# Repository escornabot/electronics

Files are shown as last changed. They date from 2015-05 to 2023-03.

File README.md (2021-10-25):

## Catalog
- [Escorna CPU][CPU01] is 50x50mm to 50x100mm board to use with Arduino Nano. It integrates keypad on board on 2x

- [Escorna_CPU_2_4][CPU240] It is a pcb that integrates an ATmega328P, a step-up (to use 1.2V batteries) and the rest of the electronics needed to build an Escornabot.

- [Arduino Shield][ARD01] is an Arduino Uno compatible
  shield ready to use with the Escornabot's motors and also integrates a keypad.

- [Cervus][CER01] is a board based on powerful ATmega32u4
  microcontroler and compatible with Arduino shields.
- [E_Keypad][KEY01] Is a 50x50mm board with 6  and 5 buttons and
  connects to any Escornabot.

- [E_KEY_BT][E_KEY_BT] Escornabot keyboard with MakeyMakey type sensors on the E_KEY_BT board.
   Any object that is minimally conductive can be used. Adjusting the value
   threshold: higher for less sensitivity, nothing needs to be changed in the
   robot firmware.

- [E_KEY_FICHA][E_KEY_FICHA] It allows the programming of Escornabot using printed or cut-out cards (cardboard ..) communicating the commands via Bluetooth.
  using @arduino Nano, easy to print, manageable and expandable to 15 "Tabs" thanks to the firmware of @caligari_pub

- [escoRnaFID][RnaFID]PCB for the project for children with visual impairment or blindness,
  developed by Angel Villanueva [@avilmaru][@avil] to control an Escornabot with RFID cards

## License

Every content in this repo, otherwise specified under subdirectories, is
licensed under [Creative Commons BY-SA][LICENSEcc] or [CERN Open Hardware Licence -W- V2][OHL-W-V2].
(by [XDeSIG][XDE01])

## To buy boards

Developer don't produce boards to sell. Under [_provider_][provider]
directory there are instructions to order yourself.

Are you a board provider? Please, send us your buyer's guide! :-)

[CPU01]: EscornaCPU
[CPU240]: https://github.com/xdesig/escornabot-electronics/tree/master/Electronics/EscornaCPU/2.x/2.40
[ARD01]: ArduinoShield
[CER01]: Cervus
[KEY01]: E_KEYPAD
[RnaFID]: escoRnaFID
[E_KEY_BT]: E_KEY_BT
[@avil]: https://twitter.com/avilmaru
[XDE01]: https://twitter.com/xdesig
[provider]: https://www.pcbway.com/project/member/?bmbno=6FE4DE76-9D11-4C
[LICENSEcc]: https://creativecommons.org/licenses/by-sa/3.0/es
[OHL-W-V2]: https://ohwr.org/project/cernohl/wikis/Documents/CERN-OHL-version-2

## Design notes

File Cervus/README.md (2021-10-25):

# Cervus 2.001

## Catalog

- [Cervus][KEY01] (by [Xdesig][XDE01]) is a 50x50mm board, it controls any Escornabot, and is an atmega development PCB (Arduino Leonardo compatible)

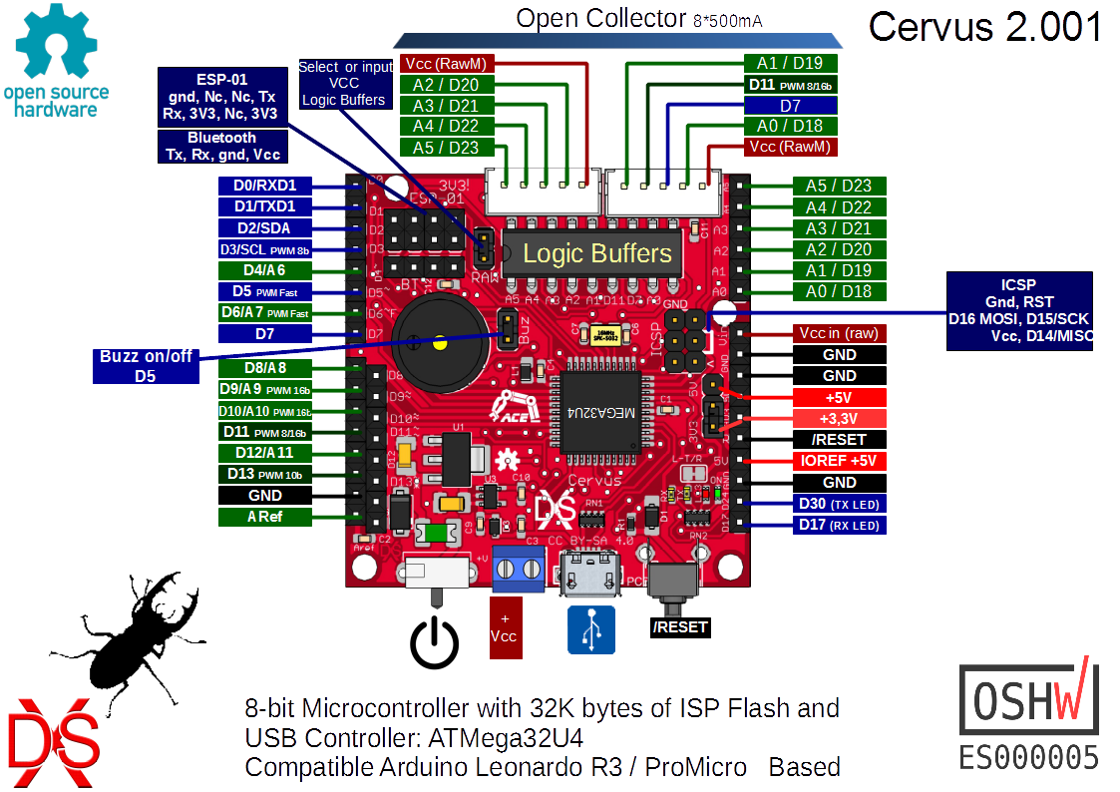
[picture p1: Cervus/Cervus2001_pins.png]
Top view


## License

Every content in this repo, otherwise specified under subdirectories, is
licensed under [Creative Commons BY-SA](LICENSE).

## To buy boards

Developers don't produce boards to sell. Under [PCBWAY]

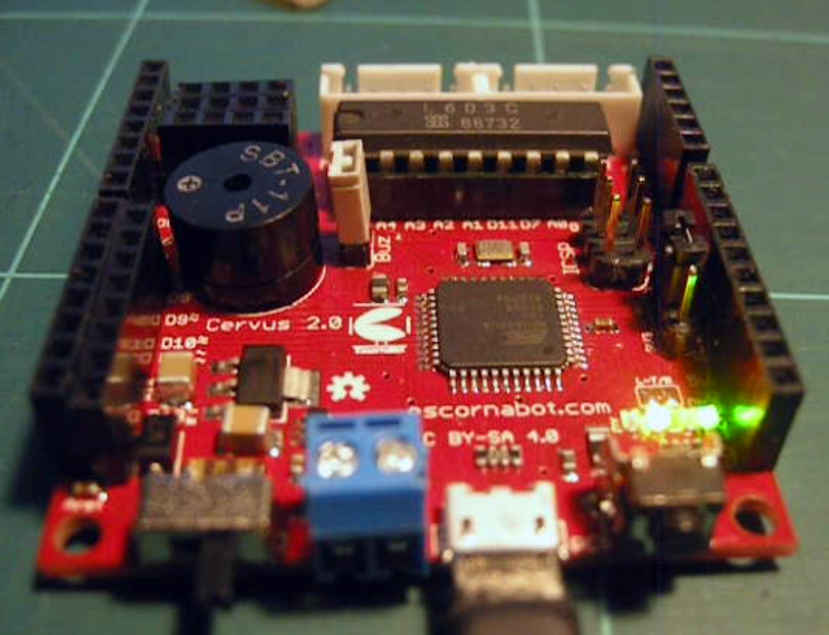
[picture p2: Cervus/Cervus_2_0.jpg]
Bottom view


[KEY01]: Keypad
[PCBWAY]: https://www.pcbway.com/project/shareproject/Cervus_Arduino_Leonardo_Coompatible.html
[XDE01]: https://twitter.com/xdesig

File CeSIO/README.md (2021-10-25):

# CeSIO Cervus Shield I/O  V 000

A pcb with all the I / O of Cervus (compatible with Arduino PCBs), available in connectors accompanied by + V and Gnd, whereby groups we can choose how we feed it: a + 5V, A + 3.3V or external V, giving the possibility to connect elements such as sensors, servos and other devices, has connector for ESP01 and Bluetooth.

It allows to use the DD05CVSA module to control a Li-ion battery.

Buy PCB in [PCBWAY]

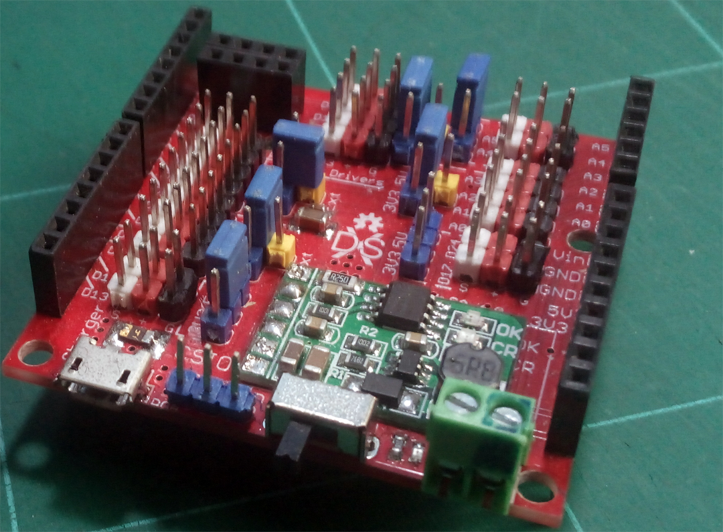
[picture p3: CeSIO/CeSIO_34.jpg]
Top view

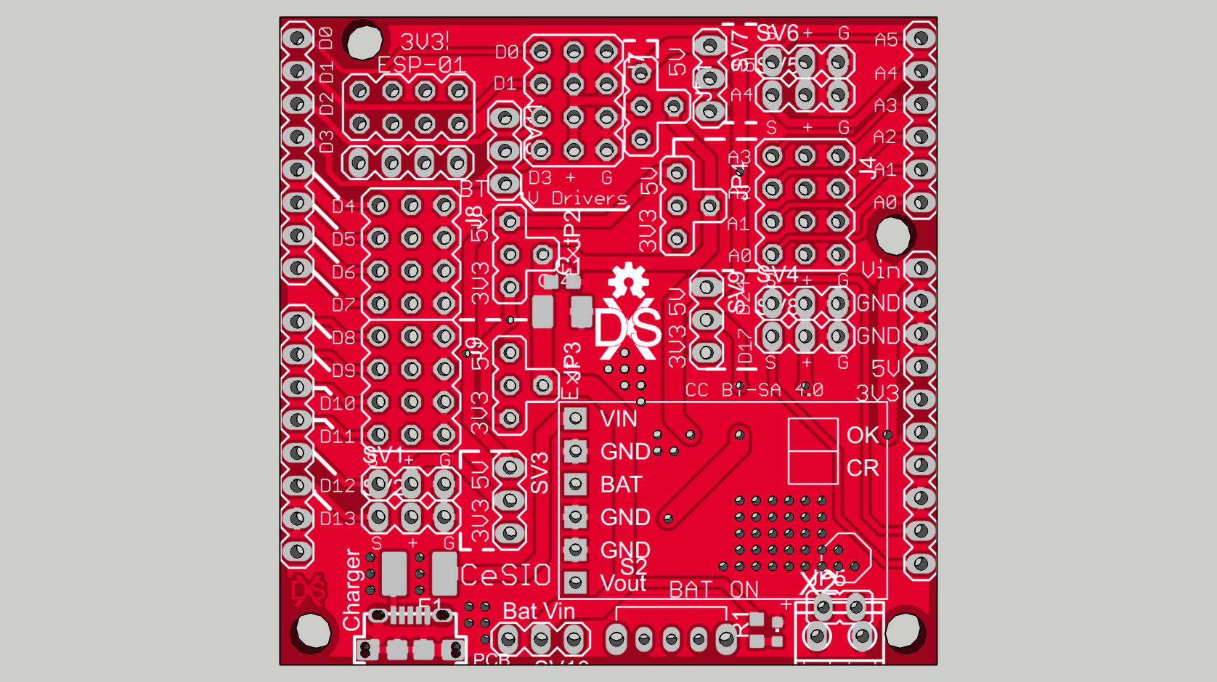
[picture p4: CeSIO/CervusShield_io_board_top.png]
Render

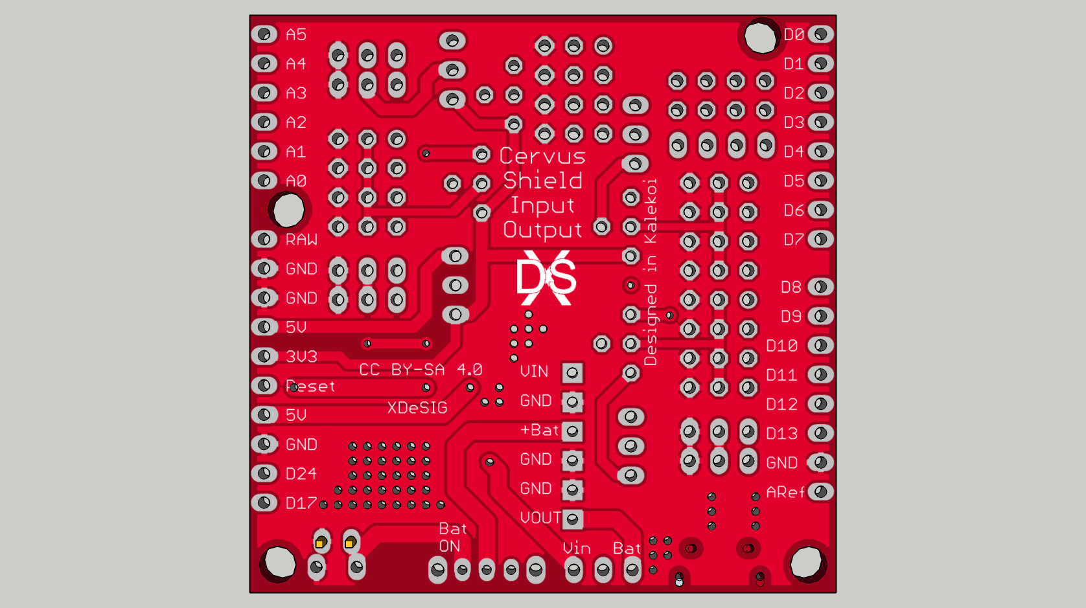
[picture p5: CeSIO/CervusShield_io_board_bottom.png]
Real


## Author and license
* Author: [XDeSIG][TWI01]
* License: [Attribution-ShareAlike 4.0 International] [CCBY-SA4.0]

<!-- links -->

[CCBY-SA4.0]: http://creativecommons.org/licenses/by-sa/4.0/
[TWI01]: https://twitter.com/xdesig
[PHT]: CeSIO_34.jpg
[RENDER]: CervusShield_io_board_top.png
[Real]: CervusShield_io_board_bottom.png
[PCBWAY]: https://www.pcbway.com/project/shareproject/CeSIO_Cervus_Shield_I_O.html

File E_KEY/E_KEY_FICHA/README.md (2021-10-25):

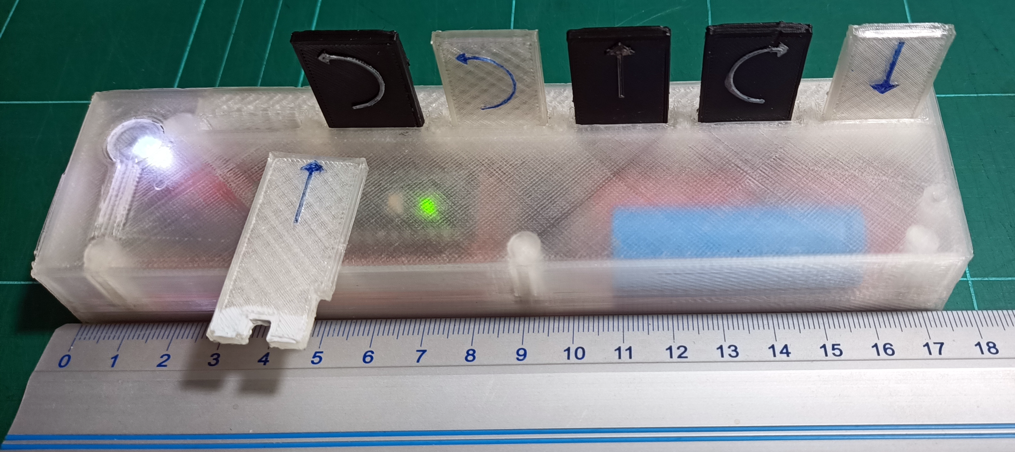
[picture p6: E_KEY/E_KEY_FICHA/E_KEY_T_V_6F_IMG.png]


## EscornabotFicha   
                     certification.oshwa.org/list.html
## E_KEY_FICHA (Tag)
It allows the programming of Escornabot using printed or cut-out cards (cardboard ..) communicating the commands via Bluetooth 
using @arduino Nano, easy to print, manageable and expandable to 15 "Tabs" thanks to the firmware of @caligari_pub.

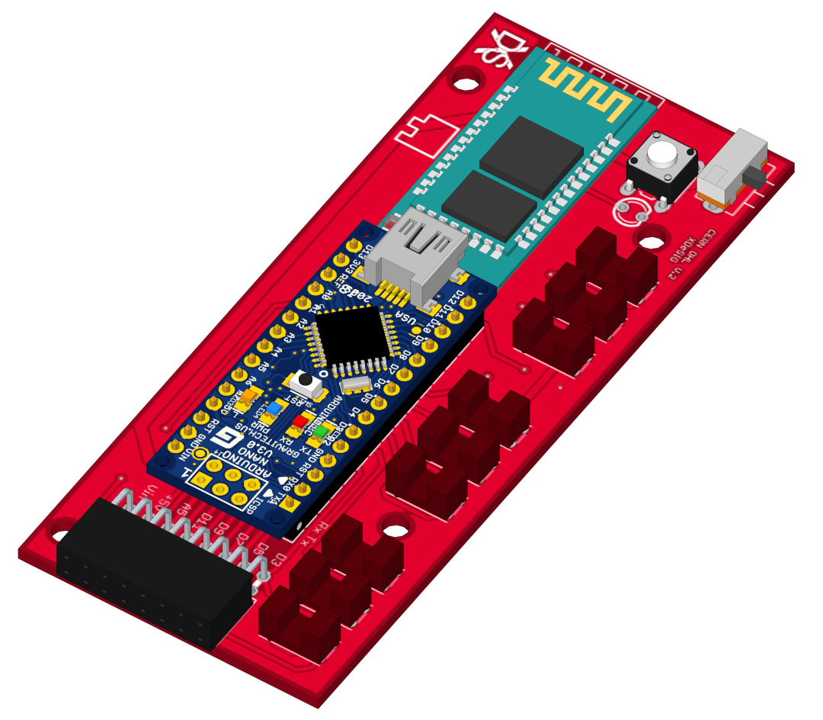
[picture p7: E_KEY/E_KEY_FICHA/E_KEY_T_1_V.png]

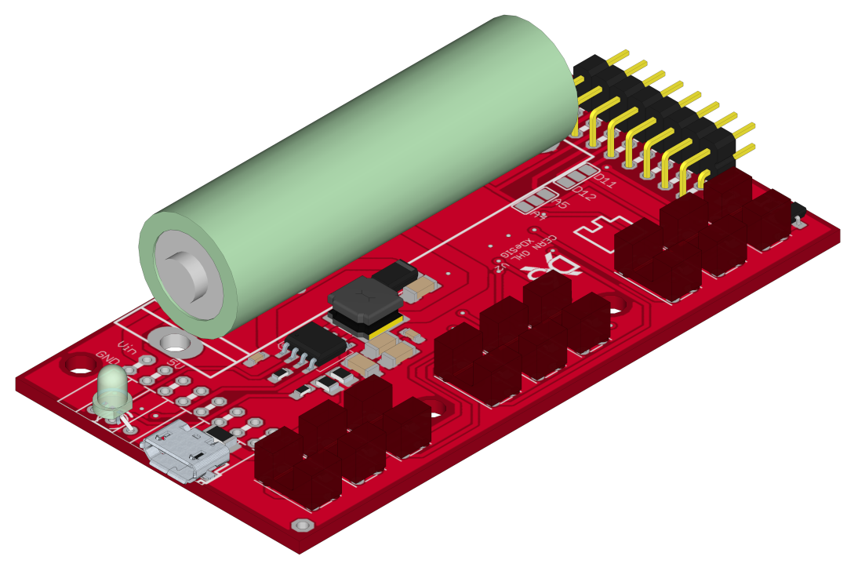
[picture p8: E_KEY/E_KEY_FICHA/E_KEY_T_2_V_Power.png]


## Number of Tags (Fichas)
To use six tags we need the PCBs E_KEY_T_1_V and E_KEY_T_2_V the latter with the power components.

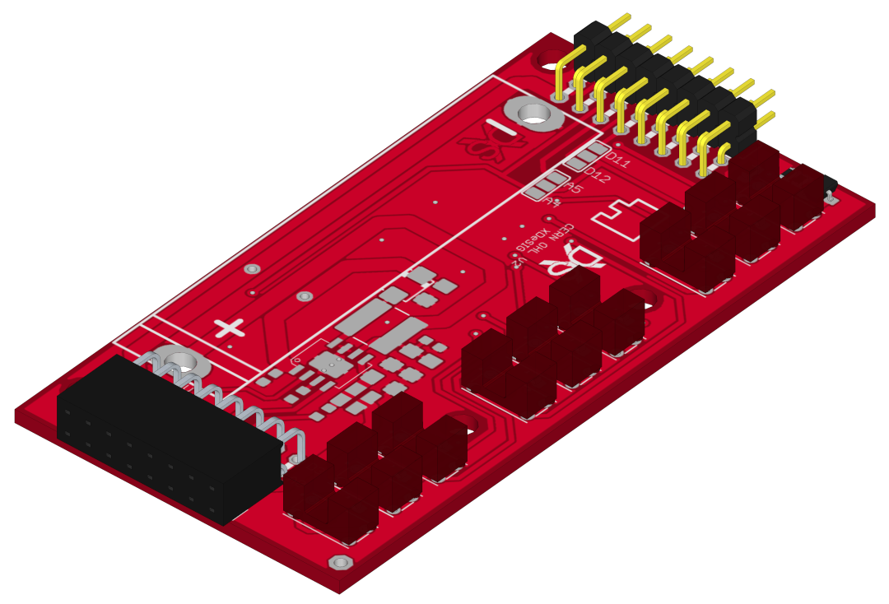
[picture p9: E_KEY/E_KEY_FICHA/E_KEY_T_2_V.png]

 If we want to have more chips (9 to 15) we will put intermediate circuits E_KEY_T_2_V without the power supply electronics.

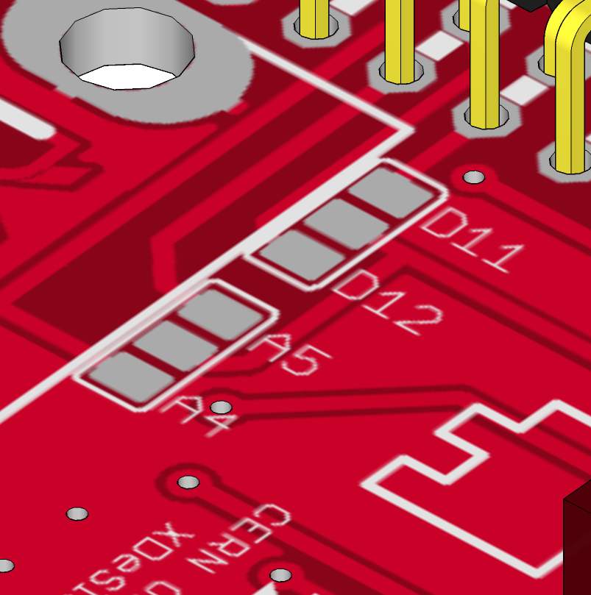
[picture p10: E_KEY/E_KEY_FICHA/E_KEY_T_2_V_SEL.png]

The selection will always be configured on the end plates, according to the firmware "configuration.h".
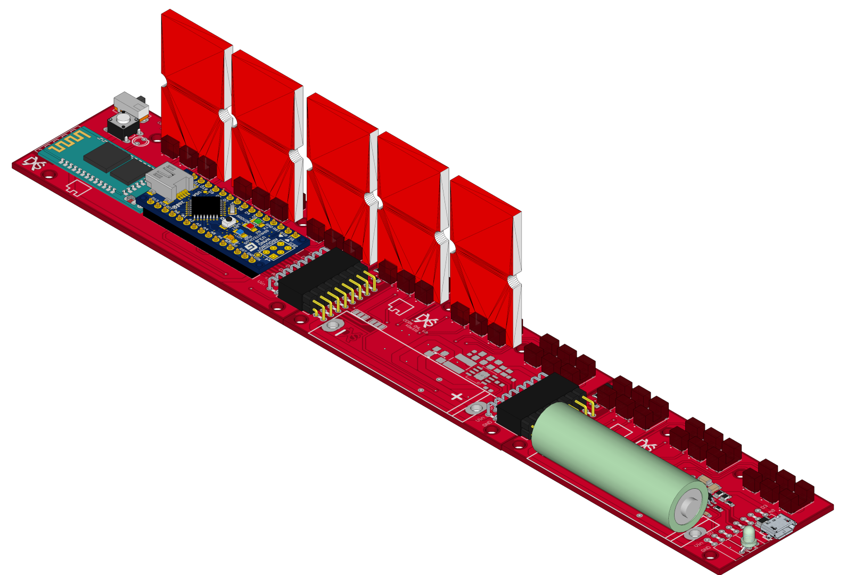
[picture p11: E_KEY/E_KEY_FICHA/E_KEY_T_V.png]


## License hardware and docu.

Every content in this repo, otherwise specified under subdirectories, is
licensed under [Creative Commons BY-SA][LICENSEcc] or [CERN Open Hardware Licence -W- V2][OHL-W-V2].
(by [XDeSIG][XDE01])

## License software.
  Copyright (C) 2020  Rafa Couto <caligari@treboada.net>
    This program is free software: you can redistribute it and/or modify
    it under the terms of the GNU General Public License as published by
    the Free Software Foundation, either version 3 of the License, or
    (at your option) any later version.
    This program is distributed in the hope that it will be useful,
    but WITHOUT ANY WARRANTY; without even the implied warranty of
    MERCHANTABILITY or FITNESS FOR A PARTICULAR PURPOSE.  See the
    GNU General Public License for more details.
    You should have received a copy of the GNU General Public License
    along with this program.  If not, see <https://www.gnu.org/licenses/>.

## Certification OSHWA [ES000024][OSHWAes000024]

## To buy boards

Developer don't produce boards to sell. Under [_provider_][provider]
directory there are instructions to order yourself.

Are you a board provider? Please, send us your buyer's guide! :-)

[imax]: https://github.com/xdesig/escornabot-electronics/blob/master/Electronics/E_KEY_BT/IMG_20180619_093516.jpg

[XDE01]: https://twitter.com/xdesig
[provider]:  http://
[LICENSEcc]: https://creativecommons.org/licenses/by-sa/3.0/es
[OHL-W-V2]: https://ohwr.org/project/cernohl/wikis/Documents/CERN-OHL-version-2
[OSHWAes000024]: https://certification.oshwa.org/es000024.html

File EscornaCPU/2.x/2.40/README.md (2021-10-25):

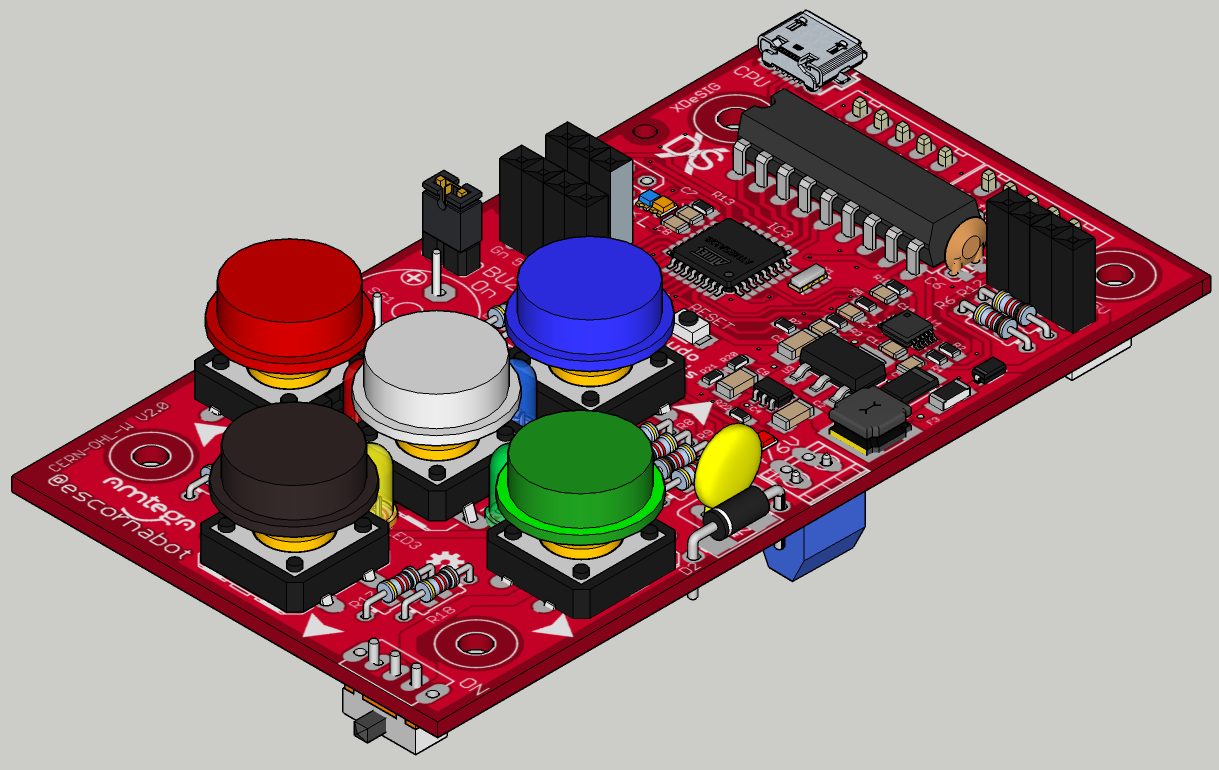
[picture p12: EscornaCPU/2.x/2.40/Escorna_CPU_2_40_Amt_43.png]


## Escorna CPU 2.4
This PCB integrates an ATmega328P, a step-up (great to use with 1.2V batteries, suggestion made by [caligari](https://github.com/rafacouto)) and the rest of the electronics needed to build a full-compatible Escornabot.
USB communications are supported by CH340E<br>
Arduino Uno, Arduino Nano compatible or ATmega minicore

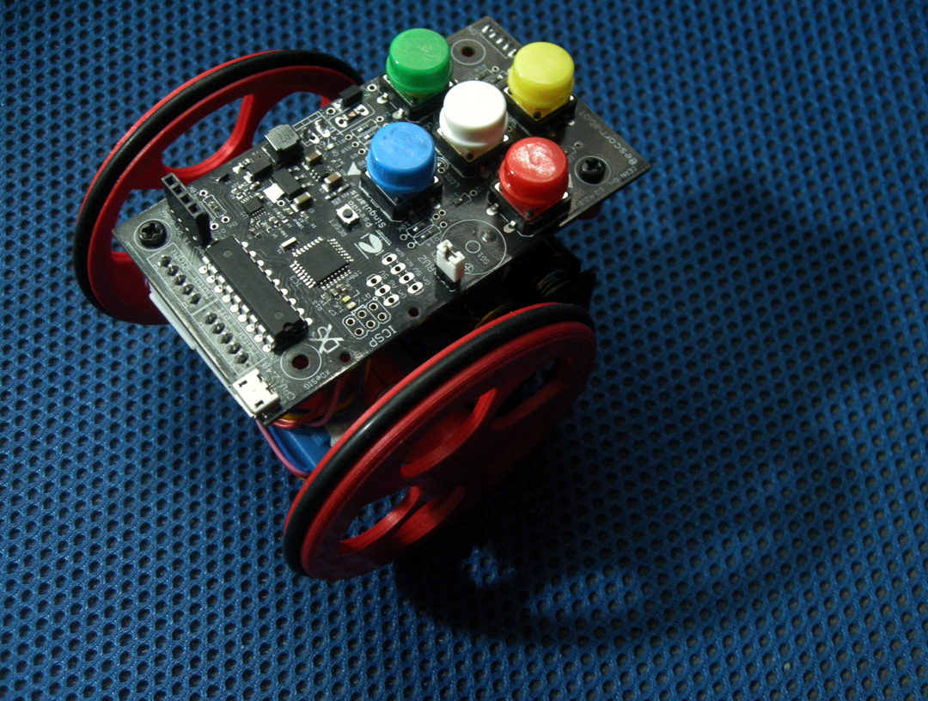
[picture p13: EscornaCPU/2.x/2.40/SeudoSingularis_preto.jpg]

   
## License



<br><br><br><br>

## Open Hardware Certification program



<br><br><br><br><br><br><br>

## To buy boards
Developer doesn't produce boards to get money. [_provider_][provider]

Are you a board provider? Please, send us your buyer's guide! xdesig@gmail.com

[XDE01]: https://twitter.com/xdesig
[provider]: https://www.pcbway.com/project/shareproject/Escorna_CPU_2_4.html
[LICENSEcc]: https://creativecommons.org/licenses/by-sa/3.0/es
[OHL-W-V2]: https://ohwr.org/project/cernohl/wikis/Documents/CERN-OHL-version-2

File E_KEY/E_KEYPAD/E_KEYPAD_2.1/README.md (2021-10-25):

# E_keyPad 2.10

## Catalog

- [Keypad][KEY01] (by [Xdesig][XDE01]) is a 50x50mm board with 5 buttons and
  connects to any Escornabot.

## License

Every content in this repo, otherwise specified under subdirectories, is
licensed under [Creative Commons BY-SA](LICENSE).

## To buy boards

Developers don't produce boards to sell. Under [PCBWAY]

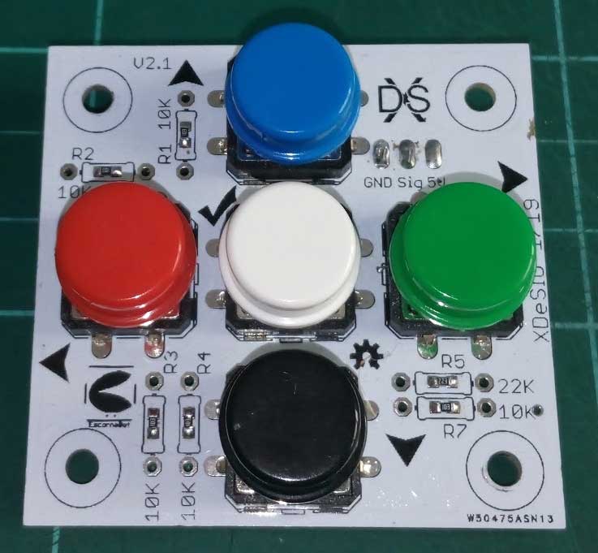
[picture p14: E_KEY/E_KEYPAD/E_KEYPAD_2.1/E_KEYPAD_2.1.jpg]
Bottom view


[KEY01]: Keypad
[PCBWAY]: https://www.pcbway.com/project/shareproject/W50475ASN5_Escorna_bot_2_1_Gerber.html
[XDE01]: https://twitter.com/xdesig

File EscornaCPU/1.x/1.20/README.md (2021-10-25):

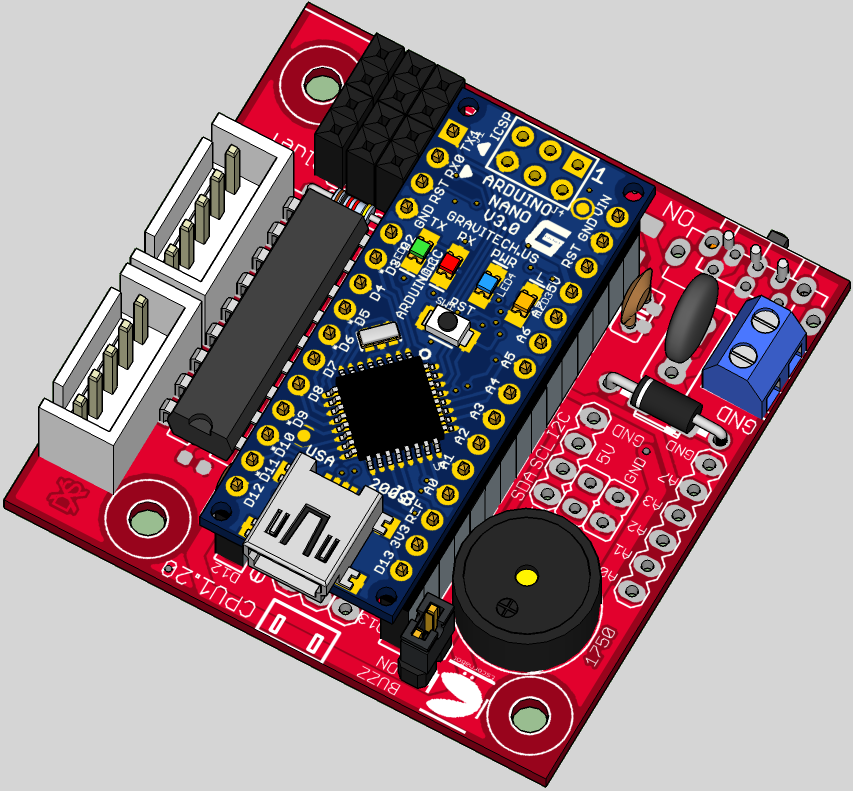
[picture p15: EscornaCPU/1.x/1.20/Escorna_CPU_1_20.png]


## Escorna CPU 1.20

It allows to include an Arduino Uno for the control of the robot, an ESP-01 or Bluetooth (for communications).
You can connect them to different keypads to manage the robot, I recommend the [E_KEYPAD_2.20]

## License

Every content in this repo, otherwise specified under subdirectories, is
licensed under [CERN Open Hardware Licence -W- V2][OHL-W-V2].
(by [XDeSIG][XDE01])

## To buy boards

Developer doesn't produce boards to get money. [provider]

Are you a board provider? Please, send us your buyer's guide! xdesig@gmail.com

[XDE01]: https://twitter.com/xdesig
[provider]: https://www.pcbway.com/project/shareproject/W50475ASN23_Escorna_CPU_1_20.html
[LICENSEcc]: https://creativecommons.org/licenses/by-sa/3.0/es
[OHL-W-V2]: https://ohwr.org/project/cernohl/wikis/Documents/CERN-OHL-version-2
[E_KEYPAD_2.20]: https://github.com/xdesig/escornabot-electronics/tree/master/Electronics/E_KEYPAD/E_KEYPAD_2.20

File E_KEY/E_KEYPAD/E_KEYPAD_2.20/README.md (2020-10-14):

# E_keyPad 2.20

## Catalog

- [Keypad][KEY01] (by [Xdesig][XDE01]) is a 50x50mm board with 5 buttons, 4 LEDs and
  connects to any Escornabot.

## License

Every content in this repo, otherwise specified under subdirectories, is
licensed under [Creative Commons BY-SA](LICENSE).
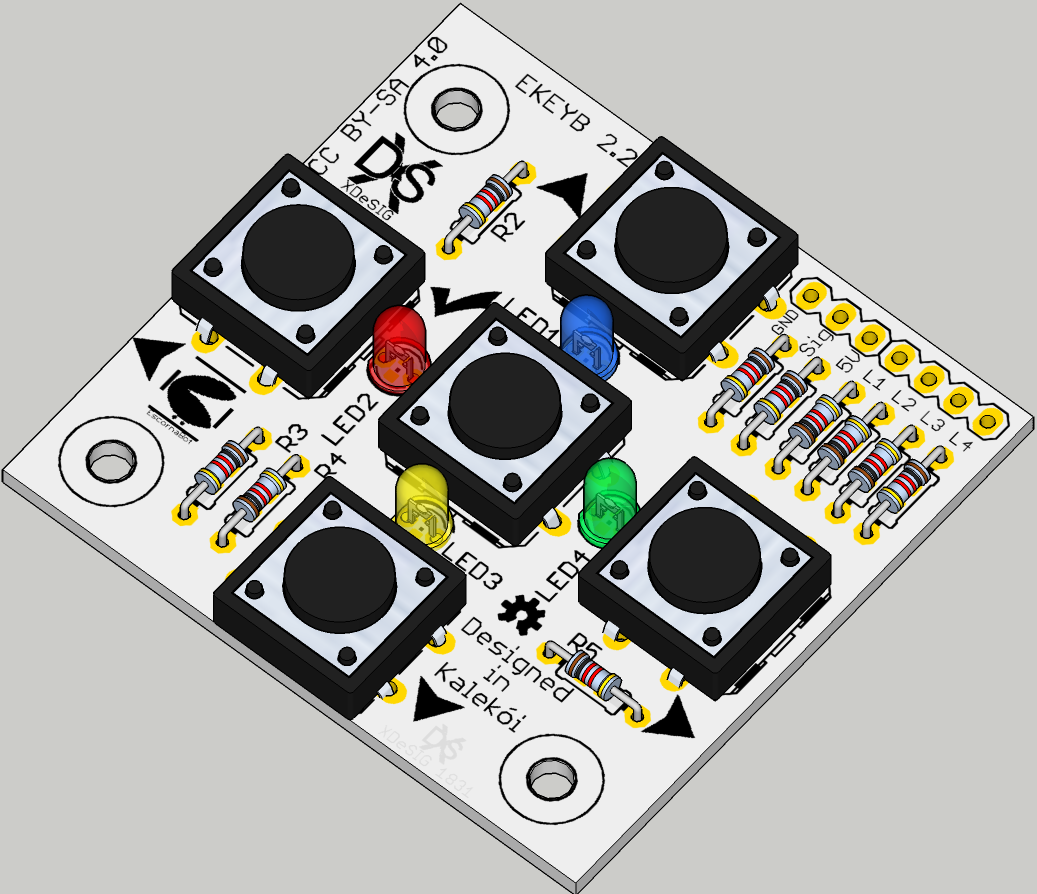
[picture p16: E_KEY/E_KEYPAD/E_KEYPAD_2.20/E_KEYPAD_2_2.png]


## To buy boards

Developers don't produce boards to sell. Under [PCBWAY]

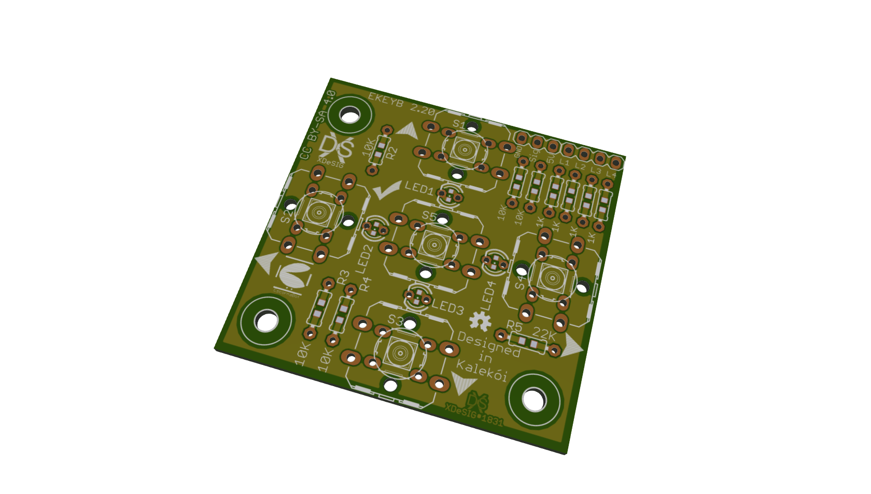
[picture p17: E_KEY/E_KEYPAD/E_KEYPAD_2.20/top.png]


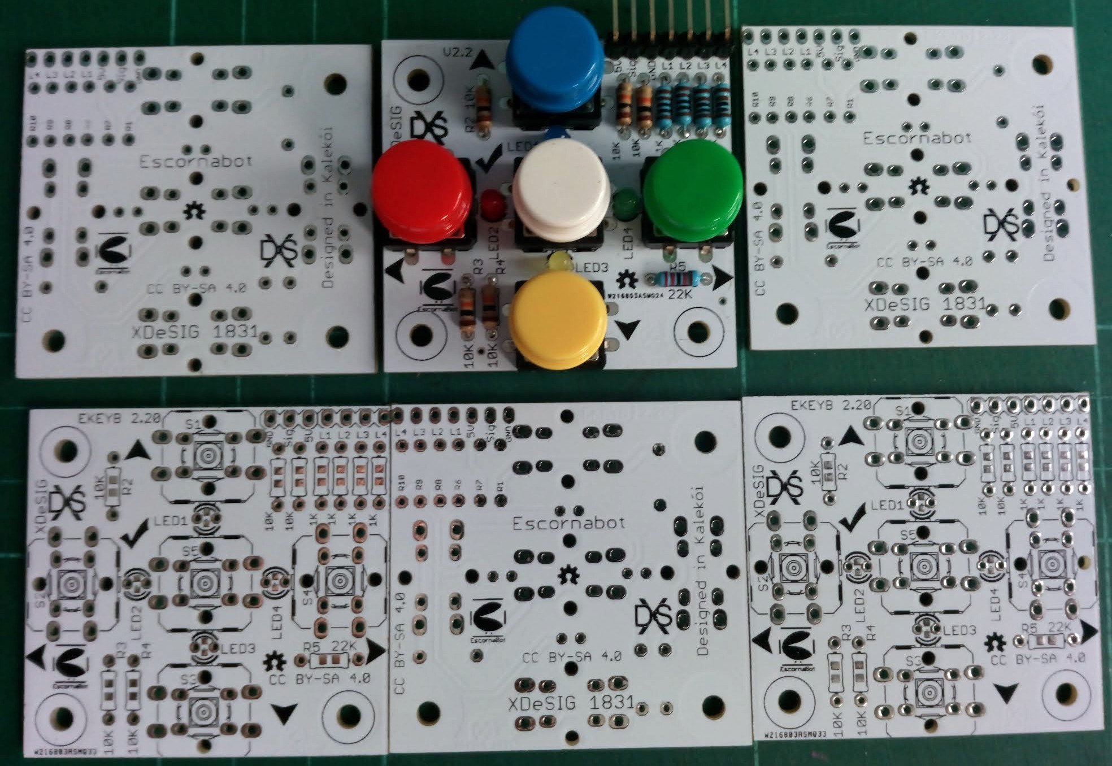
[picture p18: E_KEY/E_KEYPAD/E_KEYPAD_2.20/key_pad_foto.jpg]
Bottom view


[KEY01]: Keypad
[PCBWAY]: https://www.pcbway.com/project/shareproject/E_KEYPAD_2_2.html
[XDE01]: https://twitter.com/xdesig

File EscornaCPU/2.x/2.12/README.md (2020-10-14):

# EscornaCPU 2.12 by [XDesig][XDE01]

- Control of Escornabot through keyboard, Bluetooth HC-05, 06 and WiFi ESP-01.
- Central connector, for screen oled or I2C device.
- All components screen printed with your value.
- SMD (Surface Mount Device). or THT (through hole). Except the 3.3V and C1.2 regulator, 
- More info - [Caracteristicas\_CPU2\_12.pdf (in Galician)][NOT01]

- [Escorna\_CPU\_2\_12\_Gerber.zip (Gerber files)][GER01]
- [Escorna\_CPU\_2\_12.brd (Eagle Board)][BOA01]
- [Escorna\_CPU\_2\_12.sch (Eagle Schematics)][SCH01]
- [Escorna\_CPU\_2\_12\_ESQ.pdf (PDF Schematichs)][SCH02]
- [Escorna\_CPU\_2\_12\_measures.pdf (Board measures)][MEA01]

## License

Every content in this repo, otherwise specified under subdirectories, is
licensed under [Creative Commons BY-SA](LICENSE).

## To buy boards

Developer don't produce boards to sell. Under [PCBWAY]

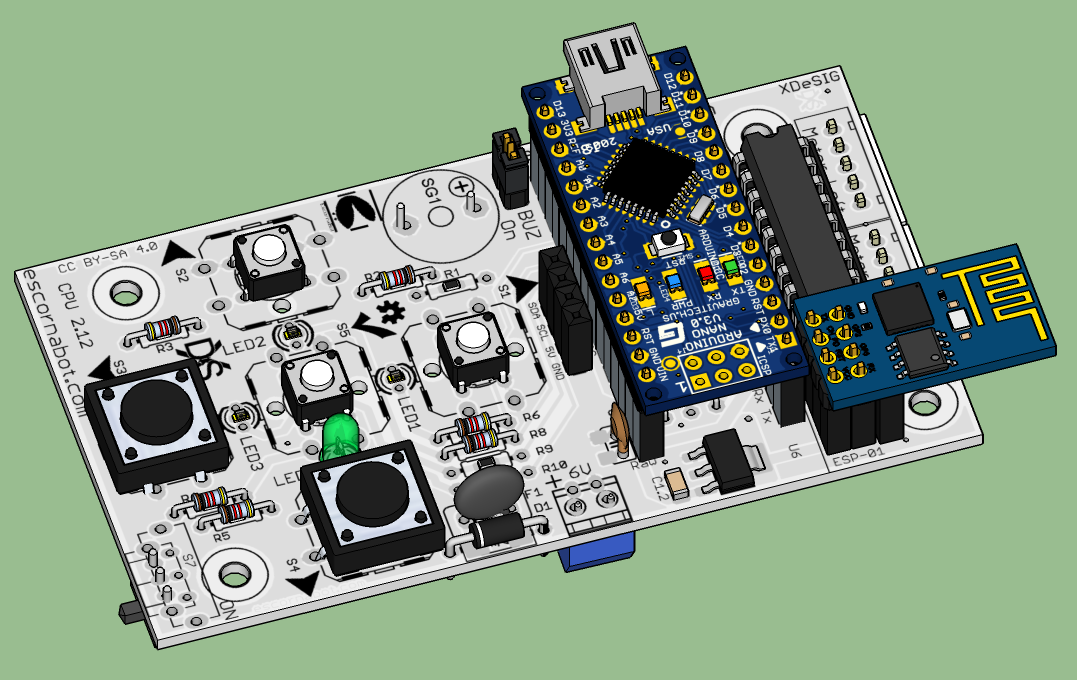
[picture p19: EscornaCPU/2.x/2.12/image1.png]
Top view

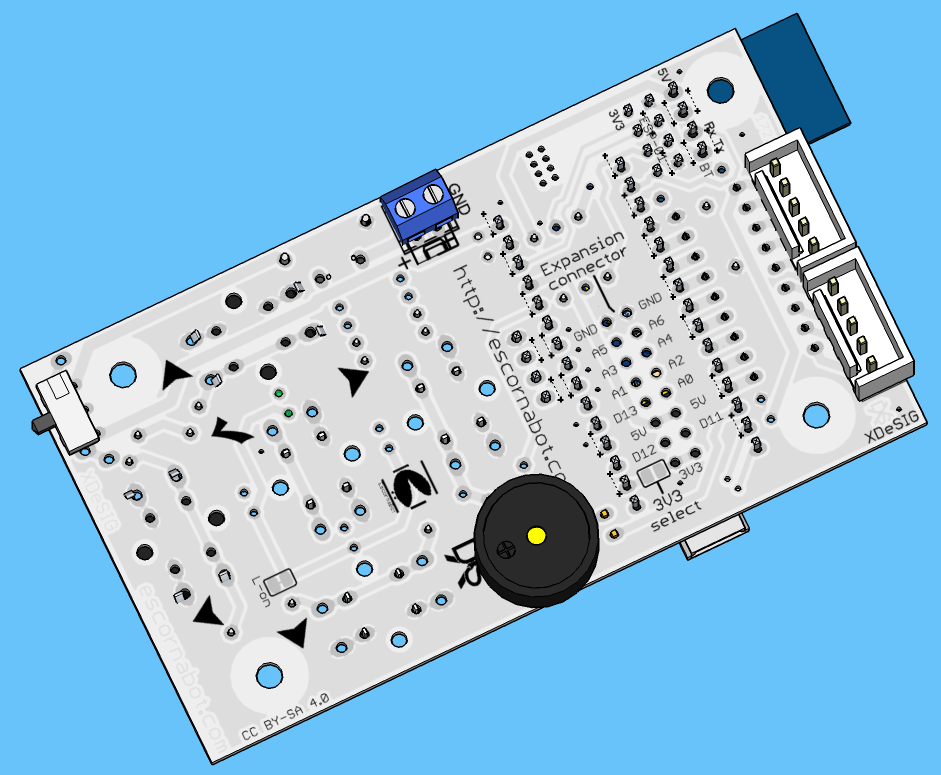
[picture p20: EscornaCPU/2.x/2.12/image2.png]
Bottom view


[GER01]: Escorna_CPU_2_12_Gerber.zip
[BOA01]: Escorna_CPU_2_12.brd
[SCH01]: Escorna_CPU_2_12.sch
[SCH02]: Escorna_CPU_2_12_ESQ.pdf
[MEA01]: Escorna_CPU_2_12_measures.pdf
[NOT01]: Caracteristicas_CPU2_12.pdf
[PCBWAY]: https://www.pcbway.com/project/shareproject/W50475ASN19_Escorna_CPU_2_12_Gerber.html
[XDE01]: https://twitter.com/xdesig

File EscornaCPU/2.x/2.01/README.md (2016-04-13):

# Escorna CPU + Keypad /  (version 2.10)

## Changes 2.10

  - Keyboard pin is A7 instead A4 so I2C interface is free to use in your projects.
  - Polarity inversion protection by diode anti-parallel and resetable fuse.
  - Power switch was moved to better position on the board 'backside'.
  - Switch compatibility with SK-12D07 and SK-12F14.
  - Keypad can use tactile switches 6mm, 12mm and 12mm with LED. See more below.
  - One of the EscornaShield connector was removed (obsolete).
  - Continuing the connector D13 - RAW (expand connections)
  - Buzzer, power connectors and drivers can be connected on both sides of the board.
  - Holes for holders continue in the same position (PCB extended 5.1mm backwards).
  - Full compatible one side, with an operative Escornabot (excepting the expansion connector).

## Tactile switches with LED

LED assignments:    --        [suggested color][wiki]

| KEY / signal| Color |
|---|---|
| UP  / A0 | Blue  |
| RIGHT / A3  | Gren  |
| DOWN / A2 | Yelow |
| LEFT / A1 | Reed  |
| GO / D13 | WiteA |

The LEDs can be disabled by cutting a small wire-jumper, you can use these outputs for other things. Reconnect with a small welding.

## Expansion connector

2.54mm double strip

| row 1 | row 2 |
|---|---|
| 3V3 | 3V3 |
| 5V | 5V |
| D13 / SCK | A0 / D14 |
| A1  / D15 | A2 / D16 |
| A3  / D17 | A4 / D18 / SDA |
| A5  / D19 / SCL | A6 / No Pullup |
| GND | GND |
|-----------------|----------------|

## Author and license

* Author: [XDeSIG][TWI01]
* License: [Creative Commons BY-SA][CCBYSA]

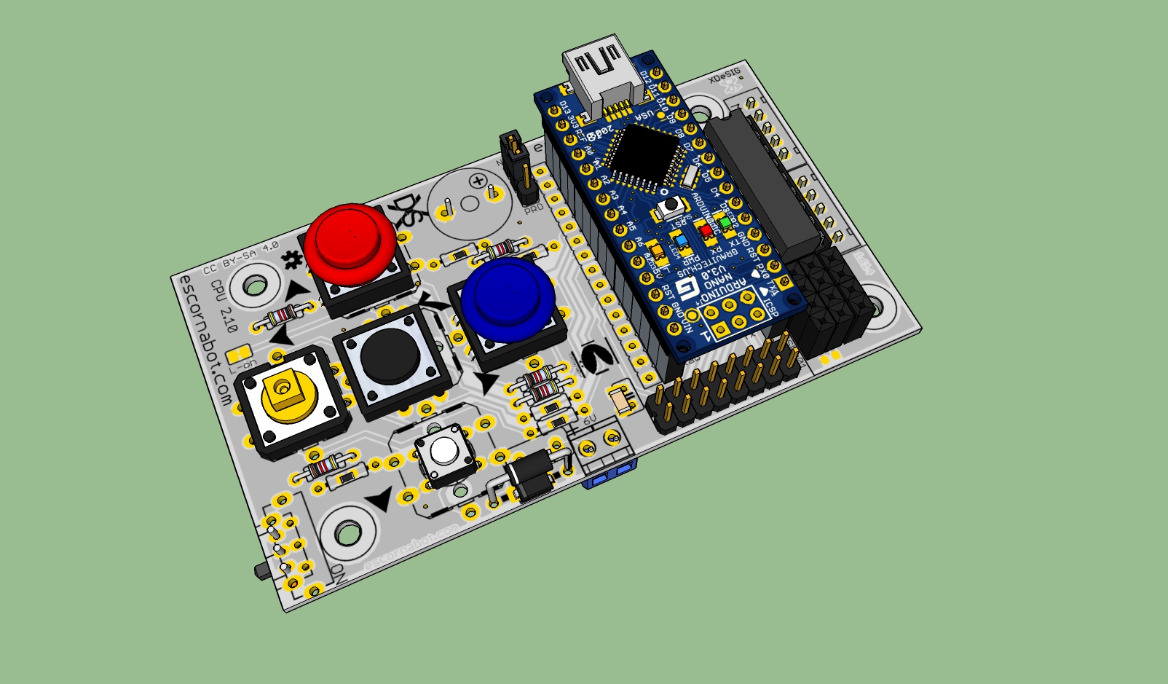
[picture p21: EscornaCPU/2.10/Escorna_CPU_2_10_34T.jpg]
Render Escorna CPU 2.10


<!-- links -->
[wiki]: https://en.wikipedia.org/wiki/Navigation_light
[CCBYSA]: http://creativecommons.org/licenses/by-sa/4.0/
[TWI01]: https://twitter.com/xdesig
[RENDER]: Escorna_CPU_2_10_34T.jpg

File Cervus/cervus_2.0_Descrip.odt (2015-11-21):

Zocalo ( tiras de pins esquerdo) 8 + 8 pins: Zocalo ( tiras de pins dereito) 6 +9 pins

Pin Atmega Leonardo Pin Atmega Leonardo

1 PD2 D0/RX 1 PF0 A5

2 PD3 D1/TX 2 PF1 A4

3 PD1 D2/SDA 3 PF4 A3

4 PD0 D3/SCL~ 4 PF5 A2

5 PD4 D4/A6~ 5 PF6 A1

6 PC6 D5 ~~ 16bits 6 PF7 A0

7 PD7 D6/A7 ~HSpeed

8 PE6 D7

8 RAW Vin

9 PB4 D8/A8 9 GND GND

10 PB5 IO9/A9 ~~ 16bits 10 GND GND

11 PB6 IO10/A10 ~~ 16bits 11 +5V +5V

12 PB7 IO11 ~~ 8/16Bits 12 +3V3 3.3V

13 PD6 IO12/A11~HSpeed 13 RESET RESET

14 PC7 IO13 ~10bits 14 +5V +5V

15 GND GND 15 D24/LTX N/C

16 Aref Aref 16 D17/LRX ( )

En grosa as conexións utilizadas por Escornabot.

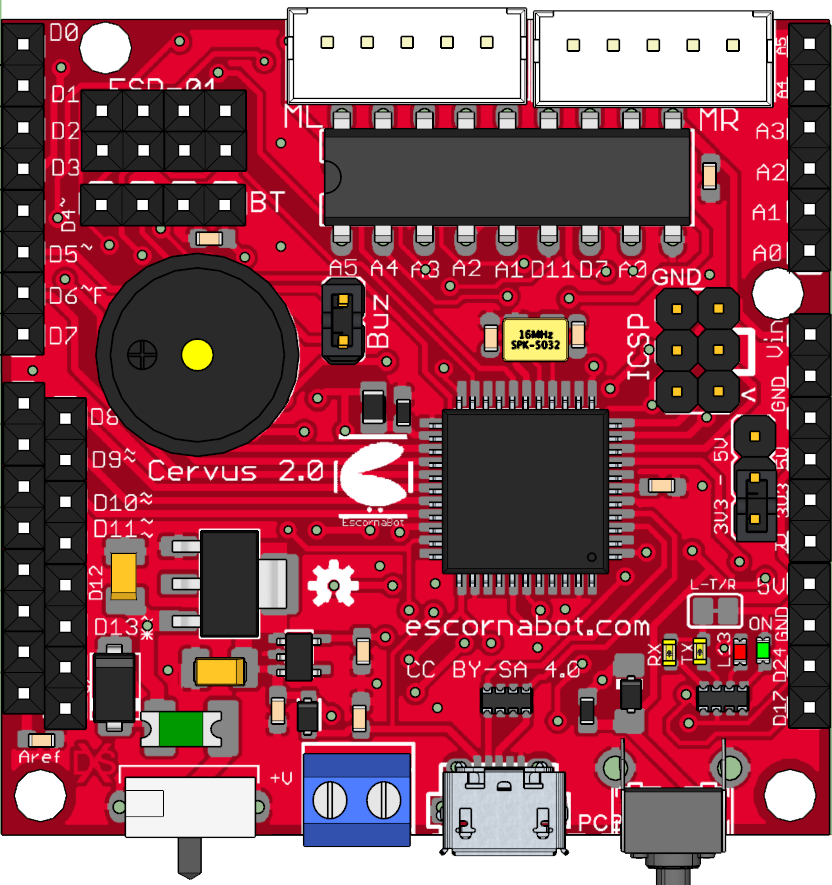
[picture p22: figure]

Selección de Alimentación 3,3V e 5V

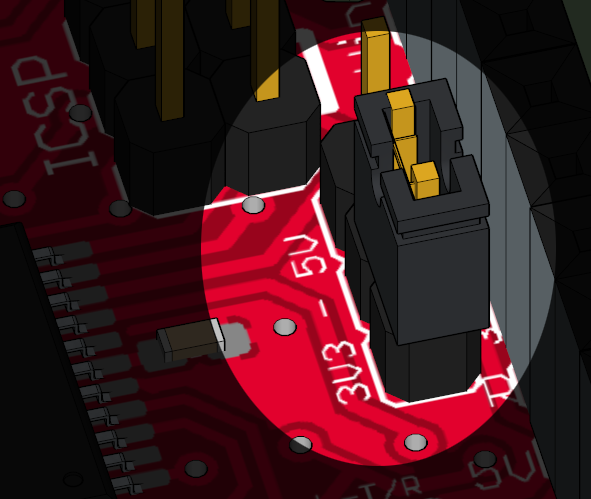
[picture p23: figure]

Posibilidade de descontar os leds ( LRX. LTX ) da placa para que non utilicen corrente das saídas ( D24, D17 ).

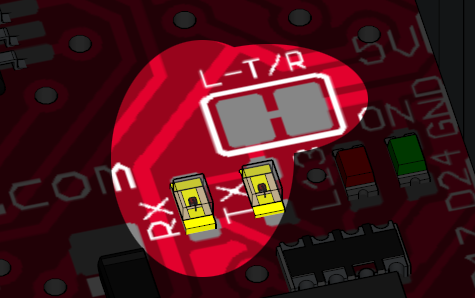
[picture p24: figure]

Igualmente co led L13 conectado a D13


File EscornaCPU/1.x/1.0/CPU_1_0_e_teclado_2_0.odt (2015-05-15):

Esquema - Escorna CPU 1.0 - Atallo os ficheiros: http://goo.gl/NUfwrV


JP1 Interruptor alimentación

JP2 podemos elixir onde conectar o Zoador,

Opcións: Sen ponte Modo silencioso (adestrar sen molestar os que durman ou estudan)

Ponte 1 – 2 Placas Pro-mini e Pro-micro

X3 conector teclado externo compatible ca versión 1 e 2, non é preciso cando se conecta o teclado Shield.

SV4 conector para modulo Bluetooth (ou outro que precise Tx e Rx)

Montaxe

Placa - Escorna CPU 1.0 -


Nota: Se se soldan os condensadores Cx non soldar os condensadores Cx.1

Dimensións Placa - Escorna CPU 1.0 -


O pad que se atopa (Baixo dereita) o lado de Tx de SV4 pode tradearse a 3mm para ter outro punto de amarre

Esquema - Escorna Shield botoneira 2.0B - Atallo os ficheiros: http://goo.gl/bZ2Vkc


Cando non utilizamos o teclado en modo shield podemos conectalo a placa CPU mediante J2. (ollo xa non teremos acceso o resto dos conectores led...)

SJ1 é un selector por soldadura para elixir a alimentación do conector J1

Opcións : 1 - 2 a tensión no pin 5 é a de entrada (RAW).

2 - 3 a tensión no pin 5 é a regulada polo arduino (5Vcc)

Montada independente Montada como Shield


Escorna CPU 1.0 e Botoneira 2.0 (shield) + Ideas

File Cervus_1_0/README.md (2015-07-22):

# Cervus version 1.0

* Author: [XDeSIG][SITE]
* License: [Creative Commons BY-SA][CCBYSA]

Render EscornaShield Keypad

[CCBYSA]: http://creativecommons.org/licenses/by-sa/4.0/
[SITE]: https://sites.google.com/site/xdesig/
[RENDER]: Cervus_1_0.jpg

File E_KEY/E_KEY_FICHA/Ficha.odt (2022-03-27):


Tamaño orientativo


Codificación da fichas (axustable en configuration.h)

W

1 2 3

Cortes

Función | Corte 1 | Corte 2 | Corte 3 | Code_
Inicio (sen ficha) | | | | 0
E | | | | 1
s | | | | 2
e | | | | 3
W | | | | 4
n | | | | 5
w | | | | 6
G | | | | 7

Escorna Ficha

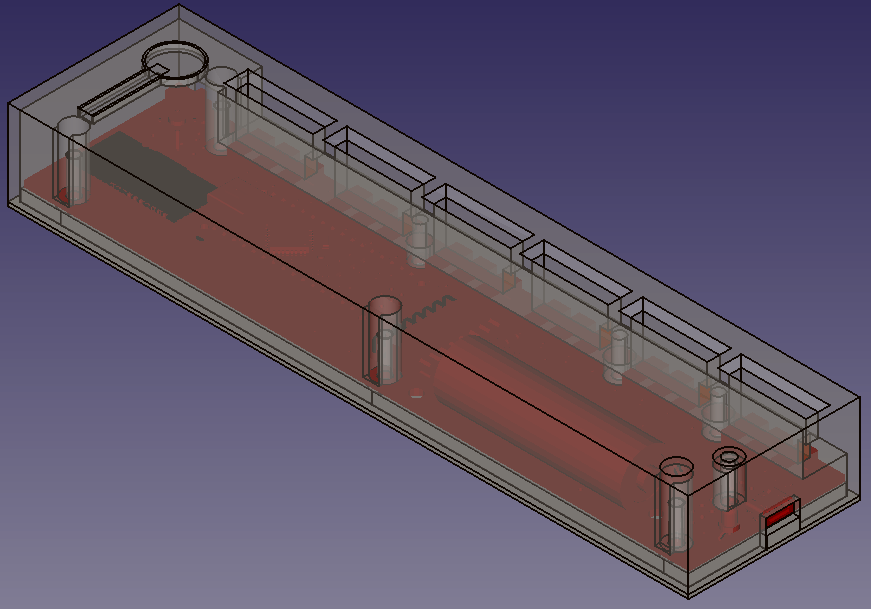
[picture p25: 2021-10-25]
E_KEY/E_KEY_FICHA/E_KEY_T_V_6F.png

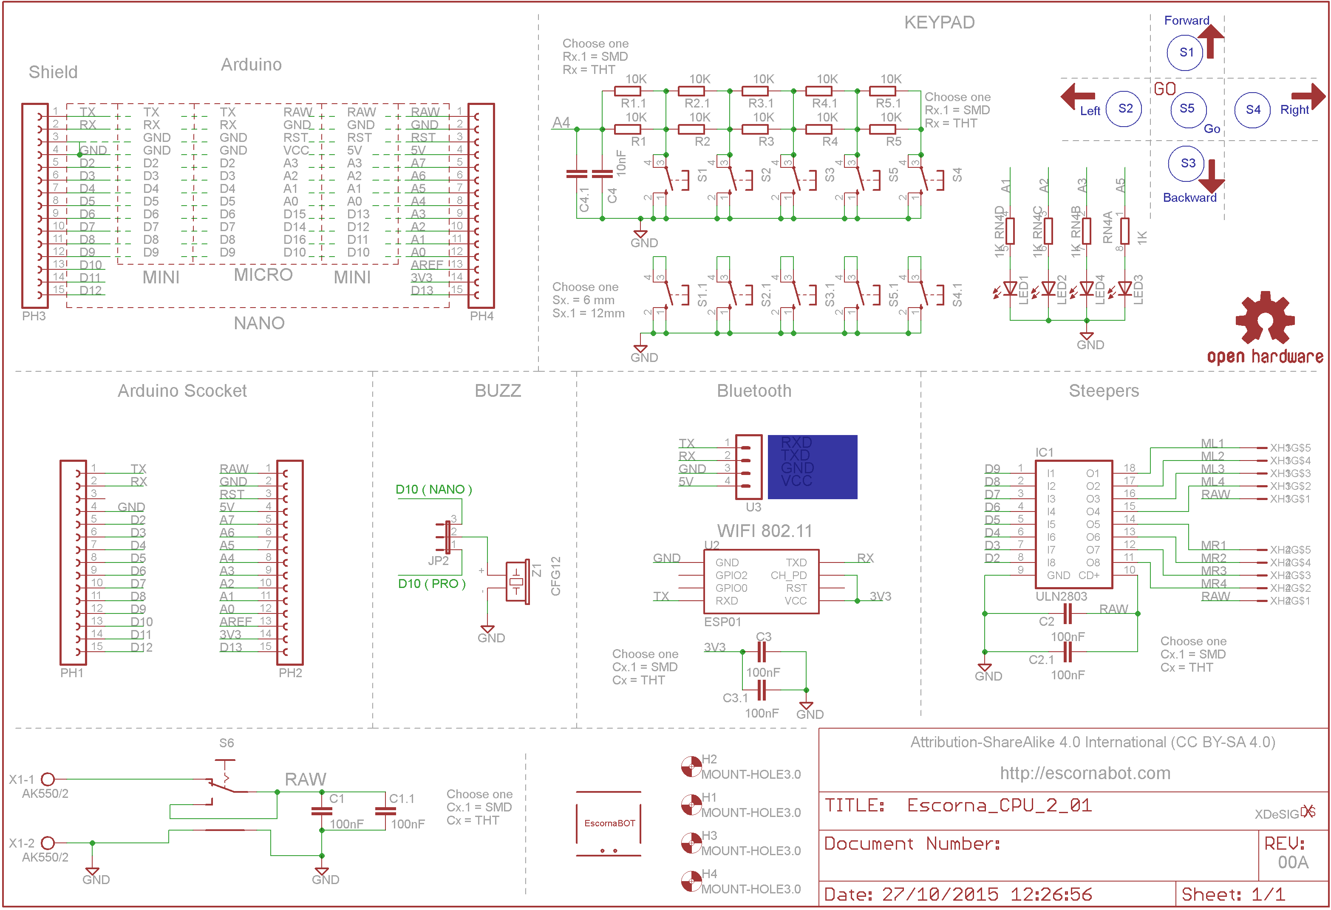
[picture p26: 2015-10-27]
EscornaCPU/2.x/2.01/Escorna_CPU_2_01_esq.png

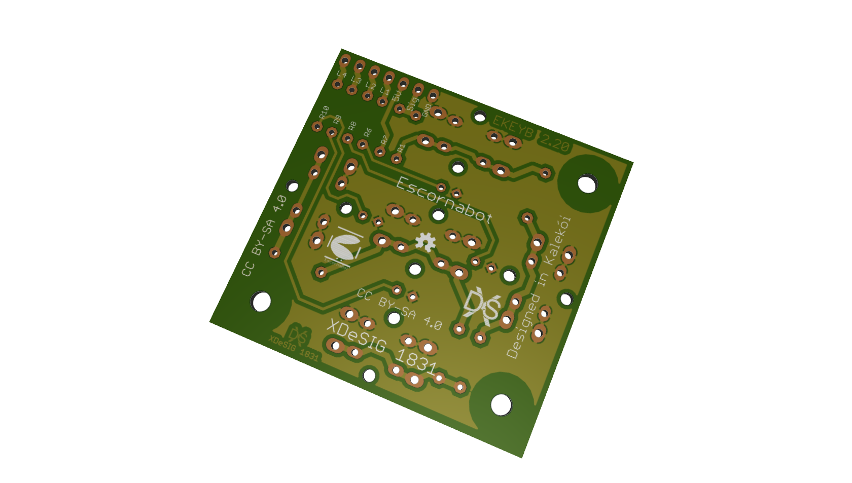
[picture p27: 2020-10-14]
E_KEY/E_KEYPAD/E_KEYPAD_2.20/bot.png

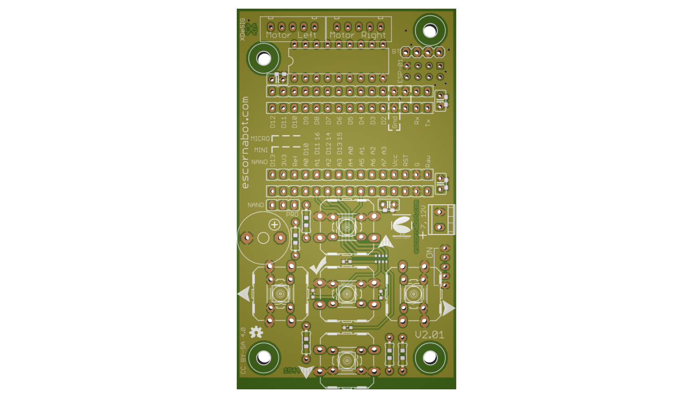
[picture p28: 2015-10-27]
EscornaCPU/2.x/2.01/Escorna_CPU_2_01_Top.png

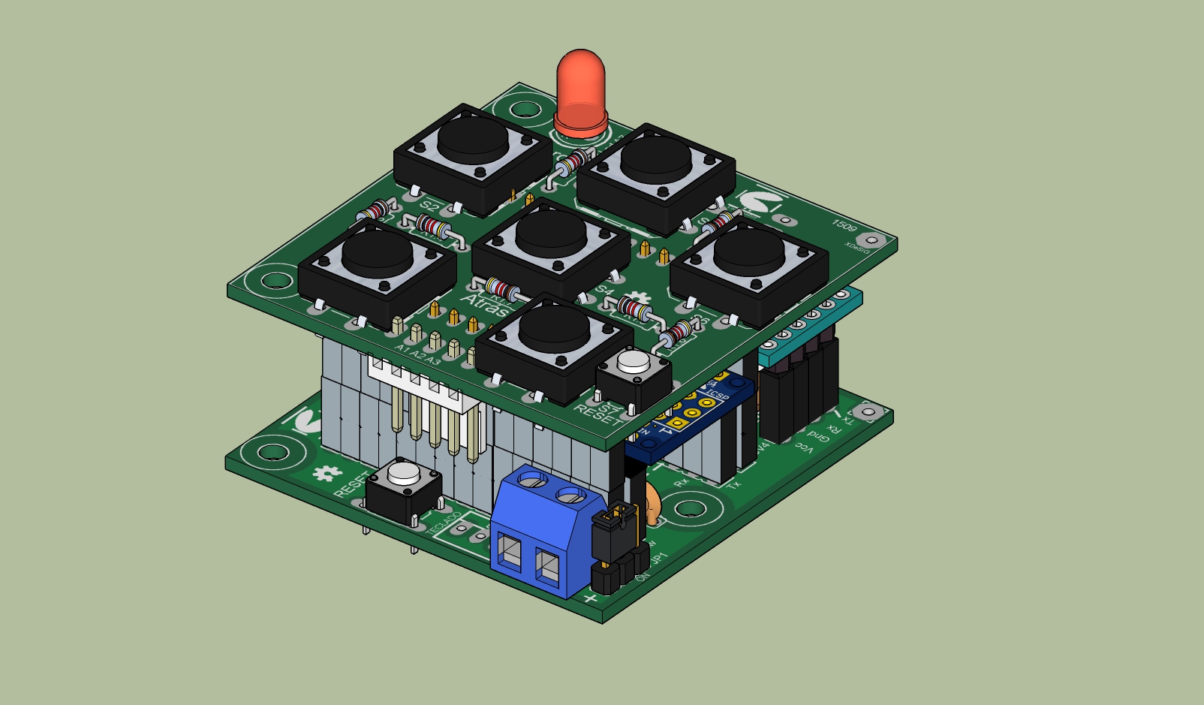
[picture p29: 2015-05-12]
EscornaCPU/1.x/1.0/Escorna_CPU_1_0 -BotoneiraShield_2_0.jpg

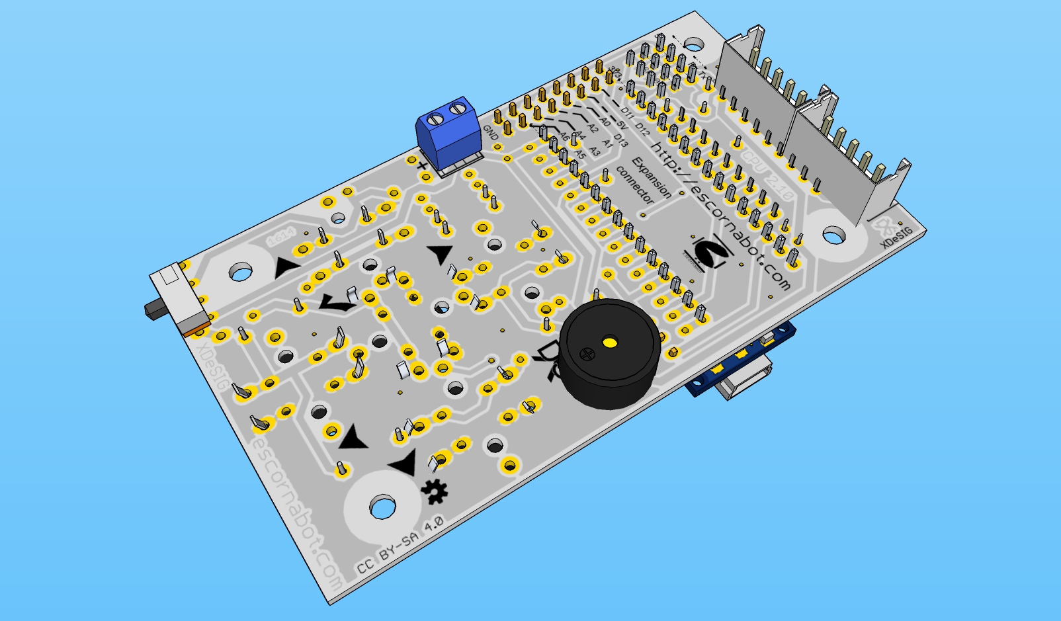
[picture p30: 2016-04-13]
EscornaCPU/2.x/2.10/Escorna_CPU_2_10_34B.jpg

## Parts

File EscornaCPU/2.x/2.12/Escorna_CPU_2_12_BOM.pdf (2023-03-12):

### Escorna_CPU_2_12_BOM

### “XDESIG”

Escornabot CPU 2.12

Qty | Value | Device | Package | Parts | Description | LCSC
5 B3F-4055 | | B3F-4055 | B3F-4055 | S1.1, S2.1, S3.1, S4.1, S5.1 | OMRON SWITCH | C84931 (https://www.lcsc.com/product-detail/Tactile-Switches_Omron-Electronics-B3F-4055_C84931.html)
4 B5B-XH-A | | B5B-XH-A | B5B-XH-A | XH1, XH2, or (XH3, XH4) | HX Connector | C5306531 (https://www.lcsc.com/product-detail/Wire-To-Board-Wire-To-Wire-Connector_JST-Sales-America-B5B-XH-AM_C5306531.html)
2 2.54 mm 1 X 15 header | | 2.54 mm 1 X 15 header | 2.54 mm 1 X 15 header | SV2, SV3 | FEMALE HEADER | C124408 (https://www.lcsc.com/product-detail/Female-Headers_Ckmtw-Shenzhen-Cankemeng-B-2200S15P-A120_C124408.html)
1 2.54 mm 2 X 4 pin | | 2.54 mm 2 X 4 pin | 2.54 mm 2 X 4 pin | U2 | FEMALE HEADER | C92271 (https://www.lcsc.com/product-detail/Female-Headers_CONNFLY-Elec-DS1023-2-4SF11_C92271.html)
1 2.54 mm 1 X 2 pin | | 2.54 mm 1 X 2 | 2.54 mm 1 X 2 | JP1 | JUMPER with cap | C5116481 (https://www.lcsc.com/product-detail/span-style-background-color-ff0-Pin-span-Headers_ZHOURI-2-54-1-2_C5116481.html)
2 2.54 mm 1 X 4 header | | MA04-1 | 2.54 mm 1 X 4 header | SV4, U3 | PIN HEADER | C2718488 (https://www.lcsc.com/product-detail/Female-Headers_BOOMELE-Boom-Precision-Elec-C2718488_C2718488.html)
2 AK550/2 | | AK550/2 | AK550/2 | X1, X1.1 | Screw terminal 3.5mm | C784940
1 SK12D07 | | SK-12D06 | SK-12D07 | S7.1 | Slide sw | C431547 (https://www.lcsc.com/product-detail/Slide-Switches_SHOU-HAN-SK12D07VG3_C431547.html)
1 ULN2803 | | ULN2803A | DIL18 | IC1 | DRIVER ARRAY | C73936 (https://www.lcsc.com/product-detail/Darlington-Transistor-Arrays_STMicroelectronics-ULN2803A_C73936.html)
1 F/CM12P | | F/CM12P | F/CM12P | SG1 | BUZZER 12mm (7mm) | C2689171 (https://www.lcsc.com/product-detail/Buzzers_S-S-SUN-1295Y-0327-45P7-6_C2689171.html)

THT Option

1 BLUE | LED3MM | LED3MM | LED1 | LED 3mm | C2895474 (https://www.lcsc.com/product-detail/Light-Emitting-Diodes-LED_XINGLIGHT-XL-302UBD_C2895474.html)
1 RED | LED3MM | LED3MM | LED2 | LED 3mm | C99771 (https://www.lcsc.com/product-detail/Light-Emitting-Diodes-LED_Everlight-Elec-204-10SURD-S530-A3-L_C99771.html)
1 YELOW | LED3MM | LED3MM | LED3 | LED 3mm | C409800 (https://www.lcsc.com/product-detail/Light-Emitting-Diodes-LED_MEIHUA-MHL3014UYTD_C409800.html)
1 GREEN | LED3MM | LED3MM | LED4 | LED 3mm | C568935 (https://www.lcsc.com/product-detail/Light-Emitting-Diodes-LED_HONGLITRONIC-Hongli-Zhihui-HONGLITRONIC-HL-304H3GD_C568935.html)
2 100nF | C-EU025-025X050 | C025-025X050 | C1, C2 | CAPACITOR | C353903 (https://www.lcsc.com/product-detail/Ceramic-Disc-Capacitors_Dersonic-CC1H104ZA1PD3F5P3003_C353903.html)
1 22K | R-EU_0204/7 | 0204/7 | R5 | RESISTOR | C61301 (https://www.lcsc.com/product-detail/Through-Hole-Resistors_UNI-ROYAL-Uniroyal-Elec-CFR0W4J0223A50_C61301.html)
8 10K | R-EU_0204/7 | 0204/7 | R1, R2, R3, R4, R7, R11, R12, R14 | RESISTOR | C61299 (https://www.lcsc.com/product-detail/Through-Hole-Resistors_UNI-ROYAL-Uniroyal-Elec-CFR0W4J0103A50_C61299.html)
1 18K | R-EU_0204/7 | 0204/7 | R13 | RESISTOR | C70811 (https://www.lcsc.com/product-detail/Through-Hole-Resistors_UNI-ROYAL-Uniroyal-Elec-CFR0W4J0183A50_C70811.html)
4 1K | R-EU_0204/7 | 0204/7 | R6, R8, R9, R10 | RESISTOR | C66649 (https://www.lcsc.com/product-detail/Through-Hole-Resistors_UNI-ROYAL-Uniroyal-Elec-CFR0W4J0102A50_C66649.html)
1 1N5817 | P4KEXX | DO41-10 | D1 | DIODE | C698892 (https://www.lcsc.com/product-detail/Schottky-Barrier-Diodes-SBD_Yangzhou-Yangjie-Elec-Tech-1N5817_C698892.html)
1 PFRA.050 | FUSETE5 | TE5 | F1 | Fuse | C1562414 (https://www.lcsc.com/product-detail/Resettable-Fuses_SCHURTER-PFRA-050_C1562414.html)

SMD Option

1 BLUE | LED 0603 | SMD 0603 | LED1.1 | LED 0603 | C434421 (https://www.lcsc.com/product-detail/Light-Emitting-Diodes-LED_Yongyu-Photoelectric-SZYY0603B_C434421.html)
1 RED | LED 0603 | SMD 0603 | LED2.1 | LED 0603 | C434419 (https://www.lcsc.com/product-detail/Light-Emitting-Diodes-LED_Yongyu-Photoelectric-SZYY0603R_C434419.html)
1 YELOW | LED 0603 | SMD 0603 | LED3.1 | LED 0603 | C434424 (https://www.lcsc.com/product-detail/Light-Emitting-Diodes-LED_Yongyu-Photoelectric-SZYY0603Y_C434424.html)
1 GREEN | LED 0603 | SMD 0603 | LED4.1 | LED 0603 | C434420 (https://www.lcsc.com/product-detail/Light-Emitting-Diodes-LED_Yongyu-Photoelectric-SZYY0603G_C434420.html)
2 100nF | 100nF/16 1206 | SMD 1206 | C1.1, C2.1 | CAPACITOR | C2858001 (https://www.lcsc.com/product-detail/Multilayer-Ceramic-Capacitors-MLCC-SMD-SMT_FH-Guangdong-Fenghua-Advanced-Tech-1206B104M101NT_C2858001.html)
1 22K | R22K | SMD 0603 | R5.1 | RESISTOR | C3016353 (https://www.lcsc.com/product-detail/Chip-Resistor-Surface-Mount_VO-SCR0603F22K_C3016353.html)
8 10K | R10K | SMD 0603 | R1.1, R2.1, R3.1, R4.1, R7.1, R11.1, R12.1, R14.1 | RESISTOR | C3017715 (https://www.lcsc.com/product-detail/Chip-Resistor-Surface-Mount_VO-SCR0603J10K_C3017715.html)
1 18K | R18K | SMD 0603 | R13.1 | RESISTOR | C3017709 (https://www.lcsc.com/product-detail/Chip-Resistor-Surface-Mount_VO-SCR0603J18K_C3017709.html)
4 1K | R1K | SMD 0603 | R6.1, R8.1, R9.1, R10.1 | RESISTOR | C3017736 (https://www.lcsc.com/product-detail/Chip-Resistor-Surface-Mount_VO-SCR0603J1K_C3017736.html)
1 SS14 | SS12 / SS32 | DO214 | D1.1 | SCHOTTKY BARRIER RECTIFIER | C2480 (https://www.lcsc.com/product-detail/Schottky-Barrier-Diodes-SBD_MDD-Microdiode-Electronics-SS14_C2480.html)
1 MF200-2 | FUSETE5 | SMD 1206 | F1.1 | PTC Resettable Fuse | C89656 (https://www.lcsc.com/product-detail/Resettable-Fuses_BOURNS-MF-NSMF200-2_C89656.html)

Optional (not required, if mounting Nano Robotdyn)

1 1117-3.3 | ASM1117-3.3 | SOT223 | U6 | IDCHIP 1117-3.3 | C5125088 (https://www.lcsc.com/product-detail/Linear-Voltage-Regulators-LDO_IDCHIP-1117-3-3_C5125088.html)
1 1uF | C-EUC1206 | C1206 | C1.2 | CAPACITOR | C2858003 (https://www.lcsc.com/product-detail/Multilayer-Ceramic-Capacitors-MLCC-SMD-SMT_FH-Guangdong-Fenghua-Advanced-Tech-1206B105M101NT_C2858003.html)

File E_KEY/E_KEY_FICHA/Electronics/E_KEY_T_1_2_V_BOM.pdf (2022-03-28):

Qty Value | Device | Package | Parts | REF. Link
1 6x6x20mm Tact Push : 6x6x20mm | : 6x6x20mm | S10
2 | FE08-2W | FE08-2W | SV3, SV2,2 | F
1 | MA08-2W | MA08-2W | SV2.1 | M
1 Led Verde 3mm | LED_LED3MM | LED_LED3MM | LED1
1 Bicolor 3mm | L-115WEGW-CA | DUOLED-A-3MM | LED2.1
3 100nF | C-EUC0603K | C0603K | C1, C2.4, C2.6
1 10uF | C-EUC1206 | C1206 | C2.7
3 22uF | C-EUC1206 | C1206 | C2.2, C2.3, C2.5
12 10K | R-EU_R0603 | R0603
1 18K | R-EU_R0603 | R0603 | R22
1 4K7 | R-EU_R0603 | R0603 | R2.8
1 1K | R-EU_R0603 | R0603 | R23
1 1K2 | R-EU_R0603 | R0603 | R2.6
20 100R | R-EU_R0603 | R0603
1 4R7 | GCNR6045-4R7NC | GCNR6045-4R7NC | L2.1
2 1R | R-EU_M0805 | M0805 | R2.2, R2.4
2 1x15 SOCKET STRIP CON-LSTA_FE15-1 | CON-LSTA_FE15 | SV1, SV2
1 10118194-0001LF/C | USB-MINI-B | USB_MICRO_B_AT | J2.2
2 AO3400A | MOSFET-NREFLOW | SOT23 | Q1, Q2.1
1 BLUETOOTH HC05 | BLUETOOTH HC05 | BLUETOOTH HC05 | M1
1 KLJ-9025-5027 | BUZZERSMD2 | Buzzer 12mm | SG1
18 RPI-441C1E | RPI-441C1E | RPI441C1
1 SK12D07 | SK12F14D | SK-12D07 | S11
1 SS34 | N-Ch 30V | DIODE_SMA | D2.1
1 TP5400 | TP5400 | ESOP8 | U2.1
1 0.5 | JFC1206-0500FS | R1206 | F2.3
1 Bat 14500-T | 14500-T | 14500-T | Bat 2.1
1 E_KEY_T_1_V | PCB
1 E_KEY_T_2_V | PCB

Ali_6x6x20 (https://es.aliexpress.com/item/32912263133.html)
C2936005 (https://www.lcsc.com/product-detail/Female-Headers_DEALON-DW254W-22-16-85_C2936005.html)
C492436 (https://www.lcsc.com/product-detail/span-style-background-color-ff0-Pin-span-span-style-background-color-ff0-Headers-span_XFCN-PZ254R-12-16P_C492436.html)
C2895465 (https://www.lcsc.com/product-detail/Light-Emitting-Diodes-span-style-background-color-ff0-LED-span_XINGLIGHT-XL-304UBC_C2895465.html)
C568938 (https://www.lcsc.com/product-detail/Light-Emitting-Diodes-span-style-background-color-ff0-LED-span_HONGLITRONIC-Hongli-Zhihui-HONGLITRONIC-HL-309S13RS12GW-C_C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)
C2168364 (https://www.lcsc.com/product-detail/Multilayer-Ceramic-Capacitors-MLCC-SMD-SMT_KEMET-C0603C104Z3VACTU_C2168364.html)
C2174304 (https://www.lcsc.com/product-detail/Multilayer-Ceramic-Capacitors-MLCC-SMD-SMT_Taiyo-Yuden-EMK316BJ106KD-T_C2174304.html)
C90146 (https://www.lcsc.com/product-detail/Multilayer-Ceramic-Capacitors-MLCC-SMD-SMT_Samsung-Electro-Mechanics-CL31A226KOHNNNE_C90146.html)
R2, R4, R6, R8, R10, R12, R14, R16,
R18, R20, R21, R2.20 | C2889366 (https://www.lcsc.com/product-detail/Chip-Resistor-Surface-Mount_VO-0603-1-10K_C2889366.html)
C2096407 (https://www.lcsc.com/product-detail/Chip-Resistor-Surface-Mount_TE-Connectivity-CRG0603F18K_C2096407.html)
C2074367 (https://www.lcsc.com/product-detail/Chip-Resistor-Surface-Mount_TE-Connectivity-CRGH0603J4K7_C2074367.html)
C2073687 (https://www.lcsc.com/product-detail/Chip-Resistor-Surface-Mount_TE-Connectivity-CRG0603F1K0_C2073687.html)
C706039 (https://www.lcsc.com/product-detail/Chip-Resistor-Surface-Mount_YAGEO-RT0603DRE071K2L_C706039.html)
R1, R3, R5, R7, R9, R11, R13, R15,
R17, R19
R2.1, R2.3, R2.5, R2.7, R2.9, R2.11,
R2.13, R2.15, R2.17, R2.19 | C2913952 (https://www.lcsc.com/product-detail/Chip-Resistor-Surface-Mount_SANYEAR-SY0603BD100RP_C2913952.html)
C439386 (https://www.lcsc.com/product-detail/Power-Inductors_GLE-GCNR6045-4R7NC_C439386.html)
C212447 (https://www.lcsc.com/product-detail/Chip-Resistor-Surface-Mount_TA-I-Tech-RMS10JT1R0_C212447.html)
Ali_1x40 (https://es.aliexpress.com/item/32719547385.html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) | + Pins (https://es.aliexpress.com/item/1005003538950566.html?pdp_pi=)
C132563 (https://www.lcsc.com/product-detail/USB-Connectors_Amphenol-ICC-10118194-0001LF_C132563.html)
C700953 (https://www.lcsc.com/product-detail/MOSFETs_HUASHUO-AO3400A_C700953.html)
Aliexpress (https://es.aliexpress.com/wholesale?catId=0&initiative_id=SB_20220328010956&SearchText=hc-05)
C556941 (https://www.lcsc.com/product-detail/Buzzers_KELIKING-KLJ-9025-5027_C556941.html)
S1, S2, S3, S4, S5, S6, S7, S8, S9
S2.1, S2.2, S2.3, S2.4, S2.5, S2.6,
S2.7, S2.8, S2.9 | C253522 (https://www.lcsc.com/product-detail/Photointerrupters-Slot-Type-Transistor-Output_ROHM-Semicon-RPI-441C1_C253522.html)
C393937 (https://www.lcsc.com/product-detail/Slide-Switches_SHOU-HAN-SK12D07VG4_C393937.html)
C432300 (https://www.lcsc.com/product-detail/Schottky-Barrier-Diodes-SBD_LGE-SS34_C432300.html)
C24154 (https://www.lcsc.com/product-detail/Battery-Management-ICs_TOPPOWER-Nanjing-Extension-Microelectronics-TP5400_C24154.html)
C136341 (https://www.lcsc.com/product-detail/Fuses_Shenzhen-JDT-Fuse-JFC1206-0500FS_C136341.html)
Ali_14500T (https://es.aliexpress.com/item/1005001340338290.html?pdp_pi=-)
EscornaFicha_1 (https://www.pcbway.com/project/shareproject/EscornaFicha_8e8114d7.html)
EscornaFicha_2 (https://www.pcbway.com/project/shareproject/EscornaFicha_2_260ae46d.html)
X2.x = component on
E_KEY_T_2_V PCB

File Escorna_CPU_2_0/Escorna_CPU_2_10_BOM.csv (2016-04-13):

Part | Value | Device | Package | Description | MF | MPN | OC_FARNELL | OC_NEWARK
C1 | 100nF/16V | C-EU025-025X050 | C025-025X050 | CAPACITOR, Multilayer Ceramic Radial LEADED
C1.1 | 100nF/16V | C-EUC1206 | C1206 | CAPACITOR, SMD 3216 Metric (1206 Imperial)
C2 | 100nF/16V | C-EU025-025X050 | C025-025X050 | CAPACITOR, Multilayer Ceramic Radial LEADED
C2.1 | 100nF/16V | C-EUC1206 | C1206 | CAPACITOR, SMD 3216 Metric (1206 Imperial)
D1 | 1N5817 | SCHOTTKY-DIODE DO41 | DO41-10 | DIODE
D1.1 | M7 | SCHOTTKY-DIODE SMA | SMA | DIODE SMA
F1 | PFRA.050 | RFUSE | PFRA.050 | PTC fuses, resettable thermistors |  |  | unknown | unknown
F1.1 | PolySwitch | PTCFUSE-1206 | R1206 | PTC fuses, resettable thermistors
IC1 | ULN2803 | ULN2803A | DIL18 | DarlingtonTransistorArrays
JP1 |  | JUMPER_JP2E | 3Fx1-2,54mm | MALE HEADER 3Pins
R1 | 10K | R-EU_0204/7 | 0204/7 | RESISTOR, ¼ Watt
R1.1 | 10K | R-EU_R0603 | R0603 | RESISTOR, SMD 1608 Metric (0603 Imperial)
R2 | 10K | R-EU_0204/7 | 0204/7 | RESISTOR, ¼ Watt
R2.1 | 10K | R-EU_R0603 | R0603 | RESISTOR, SMD 1608 Metric (0603 Imperial)
R3 | 10K | R-EU_0204/7 | 0204/7 | RESISTOR, ¼ Watt
R3.1 | 10K | R-EU_R0603 | R0603 | RESISTOR, SMD 1608 Metric (0603 Imperial)
R4 | 10K | R-EU_0204/7 | 0204/7 | RESISTOR, ¼ Watt
R4.1 | 10K | R-EU_R0603 | R0603 | RESISTOR, SMD 1608 Metric (0603 Imperial)
R5 | 10K | R-EU_0204/7 | 0204/7 | RESISTOR, ¼ Watt
R5.1 | 10K | R-EU_R0603 | R0603 | RESISTOR, SMD 1608 Metric (0603 Imperial)
R6 | 1K | R-EU_0204/7 | 0204/7 | RESISTOR, ¼ Watt
R6.1 | 1K | R-EU_R0603 | R0603 | RESISTOR, SMD 1608 Metric (0603 Imperial)
R7 | 10K | R-EU_0204/7 | 0204/7 | RESISTOR, ¼ Watt
R7.1 | 10K | R-EU_R0603 | R0603 | RESISTOR, SMD 1608 Metric (0603 Imperial)
R8 | 1K | R-EU_0204/7 | 0204/7 | RESISTOR, ¼ Watt
R8.1 | 1K | R-EU_R0603 | R0603 | RESISTOR, SMD 1608 Metric (0603 Imperial)
R9 | 1K | R-EU_0204/7 | 0204/7 | RESISTOR, ¼ Watt
R9.1 | 1K | R-EU_R0603 | R0603 | RESISTOR, SMD 1608 Metric (0603 Imperial)
R10 | 1K | R-EU_0204/7 | 0204/7 | RESISTOR, ¼ Watt
R10.1 | 1K | R-EU_R0603 | R0603 | RESISTOR, SMD 1608 Metric (0603 Imperial)
R11 | 1K | R-EU_0204/7 | 0204/7 | RESISTOR, ¼ Watt
R11.1 | 1K | R-EU_R0603 | R0603 | RESISTOR, SMD 1608 Metric (0603 Imperial)
R12 | 10K | R-EU_0204/7 | 0204/7 | RESISTOR, ¼ Watt
R12.1 | 10K | R-EU_R0603 | R0603 | RESISTOR, SMD 1608 Metric (0603 Imperial)
R13 | 18K | R-EU_0204/7 | 0204/7 | RESISTOR, ¼ Watt
R13.1 | 18K | R-EU_R0603 | R0603 | RESISTOR, SMD 1608 Metric (0603 Imperial)
S1.1 | B3F-9XXX | SWITCH-OMRON_B3F-9XXX | B3F-9XXX | OMRON SWITCH / Led
S1.2 | B3F-9XXX | SWITCH-OMRON_B3F-9XXX | B3F-9XXX | OMRON SWITCH / Led
S1.3 | B3F-9XXX | SWITCH-OMRON_B3F-9XXX | B3F-9XXX | OMRON SWITCH / Led
S1.4 | B3F-9XXX | SWITCH-OMRON_B3F-9XXX | B3F-9XXX | OMRON SWITCH / Led
S1.5 | B3F-9XXX | SWITCH-OMRON_B3F-9XXX | B3F-9XXX | OMRON SWITCH / Led
S1 |  | 10-XX | B3F-10XX | OMRON SWITCH 6mm |  | B3F-1000 | 176432 | 36M3542
S2 |  | 10-XX | B3F-10XX | OMRON SWITCH 6mm |  | B3F-1000 | 176432 | 36M3542
S3 |  | 10-XX | B3F-10XX | OMRON SWITCH 6mm |  | B3F-1000 | 176432 | 36M3542
S4 |  | 10-XX | B3F-10XX | OMRON SWITCH 6mm |  | B3F-1000 | 176432 | 36M3542
S5 |  | 10-XX | B3F-10XX | OMRON SWITCH 6mm |  | B3F-1000 | 176432 | 36M3542
S7 |  | SK12F14F | SK-12F14 | SWITCH (http://www.xiejia.com.hk) DH 17.117
S7.1 |  | SK12D07 | SK-12D07 | SWITCH (http://bit.ly/1N7X7Jb)
SV1 |  | MA08-2 | MA08-2 | PIN HEADER |  |  | unknown | unknown
SV2 |  | CON-LSTA_FE15-1 | 15Fx1-2,54mm | FEMALE HEADER 15Pins |  |  | unknown | unknown
SV3 |  | CON-LSTA_FE15-1 | 15Fx1-2,54mm | FEMALE HEADER 15Pins |  |  | unknown | unknown
SV4 |  | CON-LSTA_FE15-1 | 15Fx1-2,54mm | FEMALE HEADER 15Pins |  |  | unknown | unknown
U2 | ESP01 | Con ESP01 | 4Fx1-2,54mm | ESP8266 Wifi module 01 connector 2x4Fx1-2,54mm
U3 |  | MA04-1 | 4Fx1-2,54mm | PIN HEADER |  |  | unknown | unknown
X1 | AK550/2 | AK550/2 | AK550/2 | CONNECTOR Pin Spacing 3.5mm |  |  | unknown | unknown
X1.1 | AK550/2 | AK550/2 | AK550/2 | CONNECTOR Pin Spacing 3.5mm |  |  | unknown | unknown
XH1 |  | B5B-XH-A | B5B-XH-A | CONNECTOR HEADER XH TOP 5POS
XH2 |  | B5B-XH-A | B5B-XH-A | CONNECTOR HEADER XH TOP 5POS
Z1 | CFG12 | F/CM12P | F/CM12P | Buzzer, 5V 12mm |  |  | unknown | unknown

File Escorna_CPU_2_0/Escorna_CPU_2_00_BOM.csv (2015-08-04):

Part | Value | Device | Package | Description
C1.1 | 100nF | C-EUC0603 | C0603 | CAPACITOR, European symbol
C2.1 | 100nF | C-EUC0603 | C0603 | CAPACITOR, European symbol
C3.1 | 100nF | C-EUC0603 | C0603 | CAPACITOR, European symbol
C4.1 | 100nF | C-EUC0603 | C0603 | CAPACITOR, European symbol
IC1 | ULN2803 | ULN2803A";"DIL18 | DRIVER ARRAY
JP2 |  | JP2E | PinHead 1X03 | PinHead 1X03
LED1 |  | LED_ESML0603 | LED_SML0603 | LED
LED2 |  | LED_ESML0603 | LED_SML0603 | LED
LED3 |  | LED_ESML0603 | LED_SML0603 | LED
LED4 |  | LED_ESML0603 | LED_SML0603 | LED
PH1 |  | FE15-1 | Female Header 1x15 | FEMALE HEADER
PH2 |  | FE15-1 | Female Header 1x15 | FEMALE HEADER
PH3 |  | FE15-1 | Female Header 1x15 | FEMALE HEADER
PH4 |  | FE15-1 | Female Header 1x15 | FEMALE HEADER
R1.1 | 10K | R-EU_R0603 | R0603 | RESISTOR, European symbol
R2.1 | 10K | R-EU_R0603 | R0603 | RESISTOR, European symbol
R3.1 | 10K | R-EU_R0603 | R0603 | RESISTOR, European symbol
R4.1 | 10K | R-EU_R0603 | R0603 | RESISTOR, European symbol
R5.1 | 10K | R-EU_R0603 | R0603 | RESISTOR, European symbol
RN4 | 1K | 4R-NCAY16 | CAY16 | Array Chip Resistor
S1 |  | 10-XX | B3F-10XX | OMRON SWITCH
S2 |  | 10-XX | B3F-10XX | OMRON SWITCH
S3 |  | 10-XX | B3F-10XX | OMRON SWITCH
S4 |  | 10-XX | B3F-10XX | OMRON SWITCH
S5 |  | 10-XX | B3F-10XX | OMRON SWITCH
S6 |  | SK12F14F | SK-12F14-G | Slide SWITCH PIC
U2 | ESP01 | ESP01 | FemaleHeader 2x04 | Conector for ESP8266 Wifi module
U3 |  | MA04-1 | FemaleHeader 1x04 | PIN HEADER 4 pines Female
X1 | AK550/2 | AK550/2 | AK550/2 | CONNECTOR
XH1 |  | B5B-XH-A | B5B-XH-A | CONNECTOR
XH2 |  | B5B-XH-A | B5B-XH-A | CONNECTOR
Z1 | CFG12 | CFG12 | CFG12 | Buzer 12mm

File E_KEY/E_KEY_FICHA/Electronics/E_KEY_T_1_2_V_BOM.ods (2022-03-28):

Qty | Value | Device | Package | Parts | REF. Link
1 | 6x6x20mm Tact Push | : 6x6x20mm | : 6x6x20mm | S10 | Ali_6x6x20 (https://es.aliexpress.com/item/32912263133.html)
2 |  | FE08-2W | FE08-2W | SV3, SV2,2 | C2936005 (https://www.lcsc.com/product-detail/Female-Headers_DEALON-DW254W-22-16-85_C2936005.html) | F
1 |  | MA08-2W | MA08-2W | SV2.1 | C492436 (https://www.lcsc.com/product-detail/span-style-background-color-ff0-Pin-span-span-style-background-color-ff0-Headers-span_XFCN-PZ254R-12-16P_C492436.html) | M
1 | Led Verde 3mm | LED_LED3MM | LED_LED3MM | LED1 | C2895465 (https://www.lcsc.com/product-detail/Light-Emitting-Diodes-span-style-background-color-ff0-LED-span_XINGLIGHT-XL-304UBC_C2895465.html)
1 | Bicolor 3mm | L-115WEGW-CA | DUOLED-A-3MM | LED2.1 | C568938 (https://www.lcsc.com/product-detail/Light-Emitting-Diodes-span-style-background-color-ff0-LED-span_HONGLITRONIC-Hongli-Zhihui-HONGLITRONIC-HL-309S13RS12GW-C_C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)
3 | 100nF | C-EUC0603K | C0603K | C1, C2.4, C2.6 | C2168364 (https://www.lcsc.com/product-detail/Multilayer-Ceramic-Capacitors-MLCC-SMD-SMT_KEMET-C0603C104Z3VACTU_C2168364.html)
1 | 10uF | C-EUC1206 | C1206 | C2.7 | C2174304 (https://www.lcsc.com/product-detail/Multilayer-Ceramic-Capacitors-MLCC-SMD-SMT_Taiyo-Yuden-EMK316BJ106KD-T_C2174304.html)
3 | 22uF | C-EUC1206 | C1206 | C2.2, C2.3, C2.5 | C90146 (https://www.lcsc.com/product-detail/Multilayer-Ceramic-Capacitors-MLCC-SMD-SMT_Samsung-Electro-Mechanics-CL31A226KOHNNNE_C90146.html)
12 | 10K | R-EU_R0603 | R0603 | R2, R4, R6, R8, R10, R12, R14, R16, R18, R20, R21, R2.20 | C2889366 (https://www.lcsc.com/product-detail/Chip-Resistor-Surface-Mount_VO-0603-1-10K_C2889366.html)
1 | 18K | R-EU_R0603 | R0603 | R22 | C2096407 (https://www.lcsc.com/product-detail/Chip-Resistor-Surface-Mount_TE-Connectivity-CRG0603F18K_C2096407.html)
1 | 4K7 | R-EU_R0603 | R0603 | R2.8 | C2074367 (https://www.lcsc.com/product-detail/Chip-Resistor-Surface-Mount_TE-Connectivity-CRGH0603J4K7_C2074367.html)
1 | 1K | R-EU_R0603 | R0603 | R23 | C2073687 (https://www.lcsc.com/product-detail/Chip-Resistor-Surface-Mount_TE-Connectivity-CRG0603F1K0_C2073687.html)
1 | 1K2 | R-EU_R0603 | R0603 | R2.6 | C706039 (https://www.lcsc.com/product-detail/Chip-Resistor-Surface-Mount_YAGEO-RT0603DRE071K2L_C706039.html)
20 | 100R | R-EU_R0603 | R0603 | R1, R3, R5, R7, R9, R11, R13, R15, R17, R19 R2.1, R2.3, R2.5, R2.7, R2.9, R2.11, R2.13, R2.15, R2.17, R2.19 | C2913952 (https://www.lcsc.com/product-detail/Chip-Resistor-Surface-Mount_SANYEAR-SY0603BD100RP_C2913952.html)
1 | 4R7 | GCNR6045-4R7NC | GCNR6045-4R7NC | L2.1 | C439386 (https://www.lcsc.com/product-detail/Power-Inductors_GLE-GCNR6045-4R7NC_C439386.html)
2 | 1R | R-EU_M0805 | M0805 | R2.2, R2.4 | C212447 (https://www.lcsc.com/product-detail/Chip-Resistor-Surface-Mount_TA-I-Tech-RMS10JT1R0_C212447.html)
2 | 1x15 SOCKET STRIP | CON-LSTA_FE15-1 | CON-LSTA_FE15 | SV1, SV2 | Ali_1x40 (https://es.aliexpress.com/item/32719547385.html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) | + Pins (https://es.aliexpress.com/item/1005003538950566.html?pdp_pi=)
1 | 10118194-0001LF/C | USB-MINI-B | USB_MICRO_B_AT | J2.2 | C132563 (https://www.lcsc.com/product-detail/USB-Connectors_Amphenol-ICC-10118194-0001LF_C132563.html)
2 | AO3400A | MOSFET-NREFLOW | SOT23 | Q1, Q2.1 | C700953 (https://www.lcsc.com/product-detail/MOSFETs_HUASHUO-AO3400A_C700953.html)
1 | BLUETOOTH HC05 | BLUETOOTH HC05 | BLUETOOTH HC05 | M1 | Aliexpress (https://es.aliexpress.com/wholesale?catId=0&initiative_id=SB_20220328010956&SearchText=hc-05)
1 | KLJ-9025-5027 | BUZZERSMD2 | Buzzer 12mm | SG1 | C556941 (https://www.lcsc.com/product-detail/Buzzers_KELIKING-KLJ-9025-5027_C556941.html)
18 | RPI-441C1E | RPI-441C1E | RPI441C1 | S1, S2, S3, S4, S5, S6, S7, S8, S9 S2.1, S2.2, S2.3, S2.4, S2.5, S2.6, S2.7, S2.8, S2.9 | C253522 (https://www.lcsc.com/product-detail/Photointerrupters-Slot-Type-Transistor-Output_ROHM-Semicon-RPI-441C1_C253522.html)
1 | SK12D07 | SK12F14D | SK-12D07 | S11 | C393937 (https://www.lcsc.com/product-detail/Slide-Switches_SHOU-HAN-SK12D07VG4_C393937.html)
1 | SS34 | N-Ch 30V | DIODE_SMA | D2.1 | C432300 (https://www.lcsc.com/product-detail/Schottky-Barrier-Diodes-SBD_LGE-SS34_C432300.html)
1 | TP5400 | TP5400 | ESOP8 | U2.1 | C24154 (https://www.lcsc.com/product-detail/Battery-Management-ICs_TOPPOWER-Nanjing-Extension-Microelectronics-TP5400_C24154.html)
1 | 0.5 | JFC1206-0500FS | R1206 | F2.3 | C136341 (https://www.lcsc.com/product-detail/Fuses_Shenzhen-JDT-Fuse-JFC1206-0500FS_C136341.html)
1 | Bat 14500-T | 14500-T | 14500-T | Bat 2.1 | Ali_14500T (https://es.aliexpress.com/item/1005001340338290.html?pdp_pi=-)
1 | E_KEY_T_1_V | PCB |  |  | EscornaFicha_1 (https://www.pcbway.com/project/shareproject/EscornaFicha_8e8114d7.html)
1 | E_KEY_T_2_V | PCB |  |  | EscornaFicha_2 (https://www.pcbway.com/project/shareproject/EscornaFicha_2_260ae46d.html)
 |  |  |  | X2.x = component on E_KEY_T_2_V PCB

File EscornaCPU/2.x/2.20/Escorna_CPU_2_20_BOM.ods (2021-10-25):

Qty | Value | Device | Package | Parts | Description
4 | B5B-XH-A | B5B-XH-A | B5B-XH-A | XH1, XH2, XH3, XH4
2 | JP1E | JP1E | 1X02 | JP1, JP2 | Jumper
2 | 1x15 SOCKET STRIP | CON-LSTA_FE15-1 | CON-LSTA_FE15 | SV2, SV3 | FEMALE HEADER
4 | MA04-1 | MA04-1 | MA04-1 | U1, U3, U4, U5 | PIN HEADER
2 | MA06-1 | MA06-1 | MA06-1 | SV4, SV5 | PIN HEADER
1 | MA08-2 | MA08-2 | MA08-2 | SV1 | PIN HEADER
2 | 100nF | C-EU025-025X050 | C025-025X050 | C1, C2 | CAPACITOR
2 | 100nF | C-EUC0603K | C0603K | C1.1, C2.1 | CAPACITOR
7 | 10K | R-EU_0204/7 | 0204/7 | R1, R2, R3, R4, R10, R11, R13 | RESISTOR
7 | 10K | R-EU_R0603 | R0603 | R1.1, R2.1, R3.1, R4.1, R10.1, R11.1, R13.1 | RESISTOR
1 | 18K | R-EU_0204/7 | 0204/7 | R12 | RESISTOR
1 | 18K | R-EU_R0603 | R0603 | R12.1 | RESISTOR
4 | 1K | R-EU_0204/7 | 0204/7 | R6, R7, R8, R9 | RESISTOR
4 | 1K | R-EU_R0603 | R0603 | R6.1, R7.1, R8.1, R9.1 | RESISTOR
1 | 1uF | C-EUC0603K | C0603K | C1.2 | CAPACITOR
1 | 22K | R-EU_0204/7 | 0204/7 | R5 | RESISTOR
1 | 22K | R-EU_R0603 | R0603 | R5.1 | RESISTOR
2 | AK550/2 | AK550/2 | AK550/2 | X1, X1.1 | CONNECTOR
1 | AMS1117-3.3 | AMS1117-3.3 | SOT223 | U6 | Advanced Monolithic Systems
5 | B3F-1050 | 10-XX | B3F-10XX | S1, S2, S3, S4, S5 | OMRON SWITCH
5 | B3F-4050 | 40-XX | B3F-40XX | S1.1, S2.1, S3.1, S4.1, S5.1 | OMRON SWITCH
1 | CFG12 | F/CM12P | F/CM12P | Z1 | BUZZER
1 | ESP01 | ESP01 | ESP01 | U2 | ESP8266 Wifi module 01
1 | Blue | LED3MM | LED3MM | LED1 | LED
1 | Blue | LEDCHIPLED_0603 | CHIPLED_0603 | LED1.1 | LED
1 | Reed | LED3MM | LED3MM | LED2 | LED
1 | Reed | LEDCHIPLED_0603 | CHIPLED_0603 | LED2.1 | LED
1 | Green | LED3MM | LED3MM | LED4 | LED
1 | Green | LEDCHIPLED_0603 | CHIPLED_0603 | LED4.1 | LED
1 | Orange | LED3MM | LED3MM | LED3 | LED
1 | Orang | LEDCHIPLED_0603 | CHIPLED_0603 | LED3.1 | LED
1 | 1N5817 | P4KEXX | DO41-10 | D1 | DIODE
1 | M7 | SCHOTTKY-DIODESMA | SMA | D1.1 | Schottky Diode
1 | PFRA.050 | FUSETE5 | TE5 | F1 | Fuse
1 | PolySwitch | PTCFUSE-1206 | R1206 | F1.1 | PTC fuses, resettable thermistors
1 | SK12D07 | ESCORNA_SK12F14D | ESCORNA_SK-12D07 | S7.1
1 | SK12F14 | ESCORNA_SK12F14F | ESCORNA_SK-12F14-G | S7
1 | ULN2803 | ULN2803A | DIL18 | IC1 | DRIVER ARRAY
Yelow = SMD components

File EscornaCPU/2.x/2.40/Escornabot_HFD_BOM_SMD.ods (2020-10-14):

So compoñentes SMD
Qty | Value | Device | Package | Parts | Description | TME Ref | TME_EUROS_UNIT | Tot
1 | 4.7uH | L-EUL4532P | L4532P | L1 | SMD; 4,7uH; Itrabajo: 3,7A; 40,3mΩ; 6x5,9x4,5mm | DJNR6045-4R7 (https://www.tme.eu/es/details/djnr6045-4r7/chokes-smd-de-potencia/ferrocore/) | 0,1559 € | 0,156 €
5 | 100nF | 100nF_0603 | C0603 | C1, C4, C5, C8, C11 |  | 06033G104ZAT2A | 0,0159 € | 0,080 €
1 | USB MICRO | MYCON2_USB-MINI-B | CON2_USB_MICRO_B_AT | J2 | Connetor | 10118194-0001LF/C | 0,2438 € | 0,244 €
1 | 10uF | C-EUC1206 | C1206 | C3 | CAPACITOR | 12063C106KAT2A | 0,6260 € | 0,626 €
1 | 1PS76SB10.115 | DIODESOD | SOD-323 | D3 |  | 1PS76SB10.115 | 0,0690 € | 0,069 €
1 | 200R | R-EU_R0603 | R0603 | R21 | Resistor 0603 1% | CRCW0603200RFKTABC | 0,0236 € | 0,024 €
2 | 22uF | C-EUC1206 | 1206 | C2, C9 | MLCC; 22uF; 16V; X5R; | 1206X226K100CT | 0,2310 € | 0,462 €
1 | ATMEGA328P-AU | 0265_ATMEGA328P-AU | TQFP32-08 | IC3 | Flash: 32kB; TQFP44 | ATMEGA32U4-AU | 3,6100 € | 3,610 €
1 | LD1117S50TR | LD1117S50TR | SOT-223 | IC1 | 5V reg | LD1117S50TR | 0,2400 € | 0,240 €
1 | B3U-1000P | 0173_IT-1185AP1C-160G-G_T&R | SMD_157SW | S6 |  | B3U-1000PM | 0,5100 € | 0,510 €
1 | CH340E | CH340E | MSOP10 | U1 | USB 2.0 2Mbps | CH340E | 0,5200 € | 0,520 €
1 | MFFSMF050 | PTC | 1206 | F2 | PTC; 500mA; Imax: 100A; Carc: 1206 | 0ZCJ0050AF2E | 0,1499 € | 0,150 €
1 | SS14 | SS14 | SMA | D1 | Schottky; SMD; 40V; 1A; SMA | SS14-DC | 0,0270 € | 0,027 €
1 | SX1308 | SX1308 | SOT23-6 | IC4 | SX1308 switches at. 1.2MHz | SX1308 | 0,1500 € | 0,150 €
 |  |  |  |  |  |  |  | 6,867 €

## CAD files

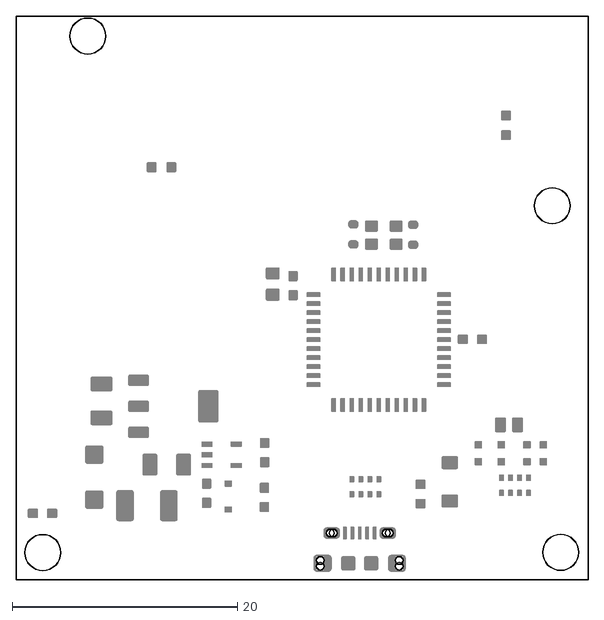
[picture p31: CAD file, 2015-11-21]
Cervus/cervus_2_0_TCream.dxf
50.8 x 50.1

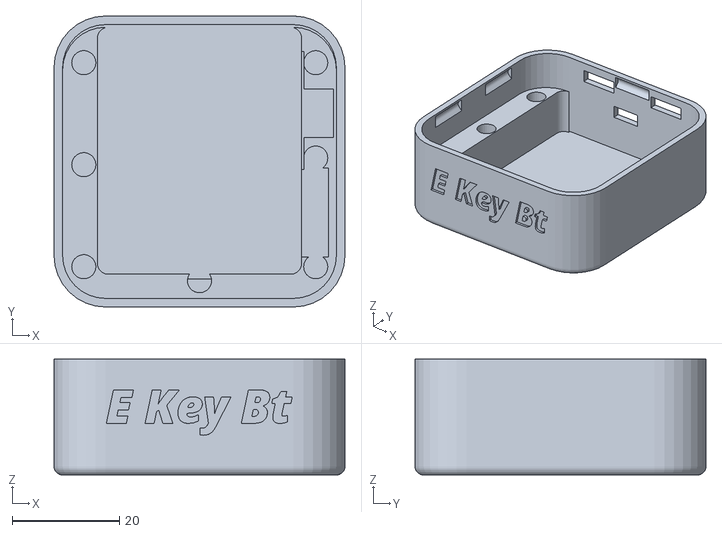
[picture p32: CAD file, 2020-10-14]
E_KEY/E_KEY_BT/3D/Base_E_Key_BT.stl
54.2 x 54.2 x 21.6

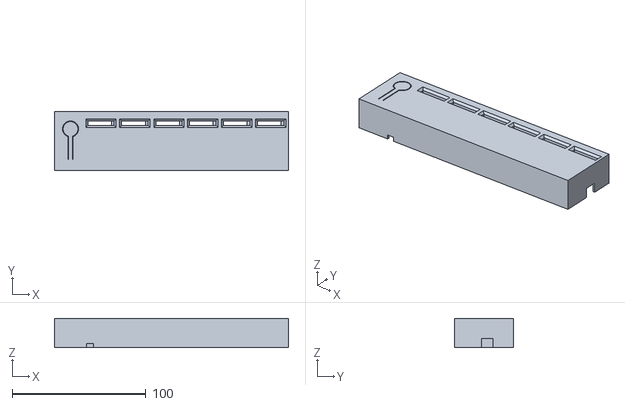
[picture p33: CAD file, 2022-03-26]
E_KEY/E_KEY_FICHA/3D/E_KEY_T_V_CaseT_6F.stl
175.0 x 44.0 x 22.0

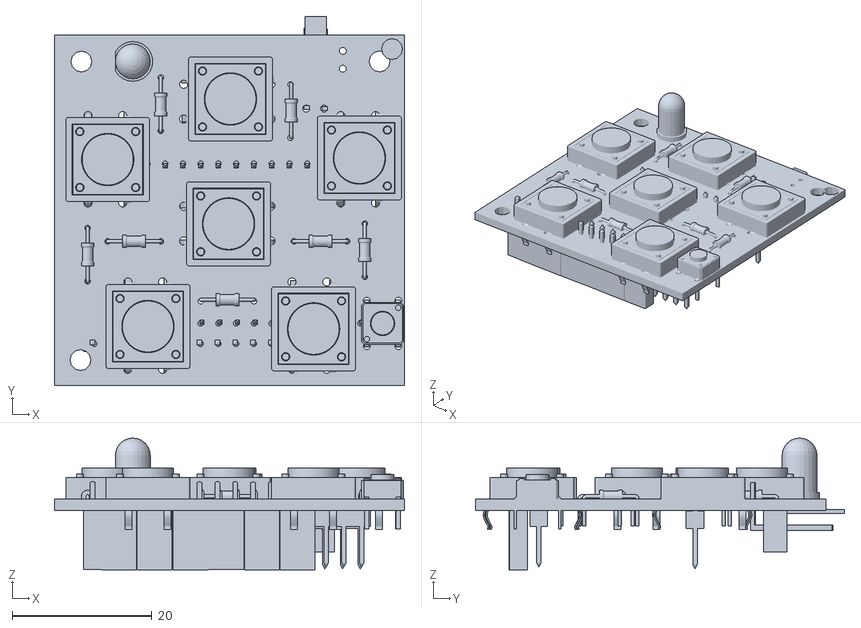
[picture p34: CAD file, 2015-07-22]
E_KEY/E_KEYPAD/E_KEYPAD_2.0D/Escorna_Shield_botoneira_2_0D.stl
50.2 x 52.8 x 18.9

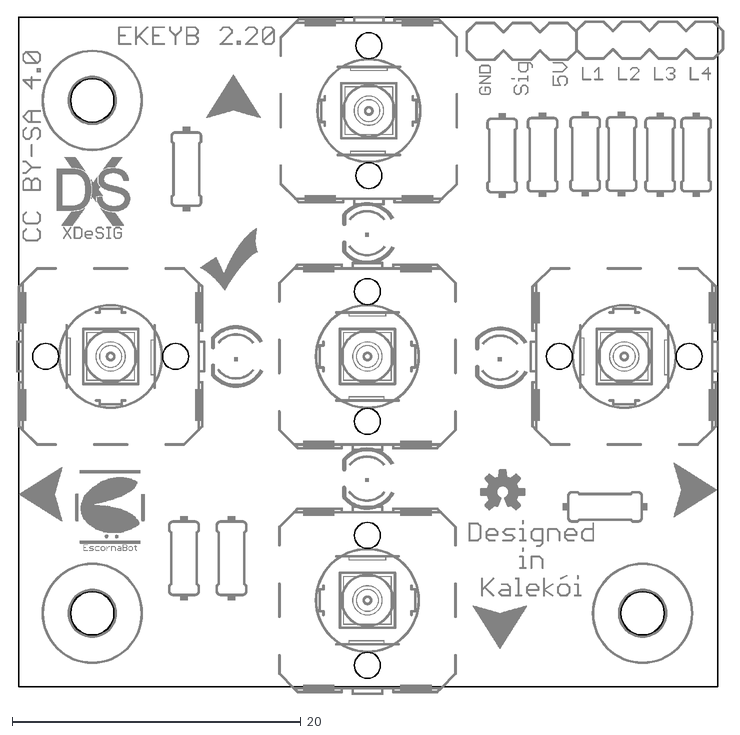
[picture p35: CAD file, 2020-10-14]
E_KEY/E_KEYPAD/E_KEYPAD_2.20/E_KEYPAD_2_2_top.dxf
49.0 x 47.0

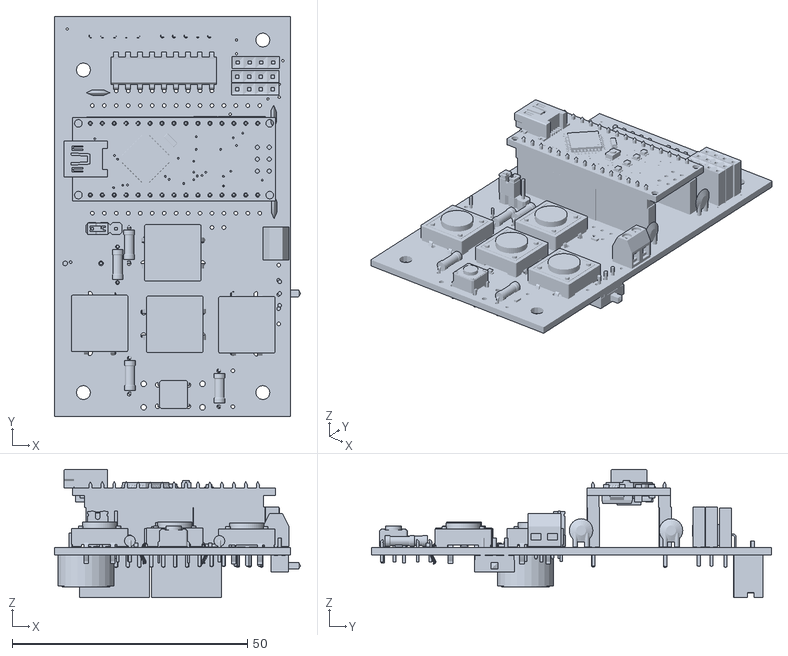
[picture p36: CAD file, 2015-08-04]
EscornaCPU/2.x/2.01/Escorna_CPU_2_01_3D.stl
52.3 x 85.0 x 27.2

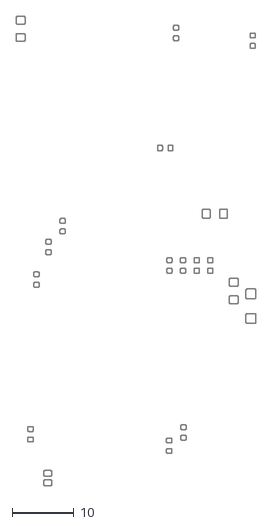
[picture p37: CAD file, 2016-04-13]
EscornaCPU/2.x/2.10/Escorna_CPU_2_10_Cream.dxf
38.9 x 76.3

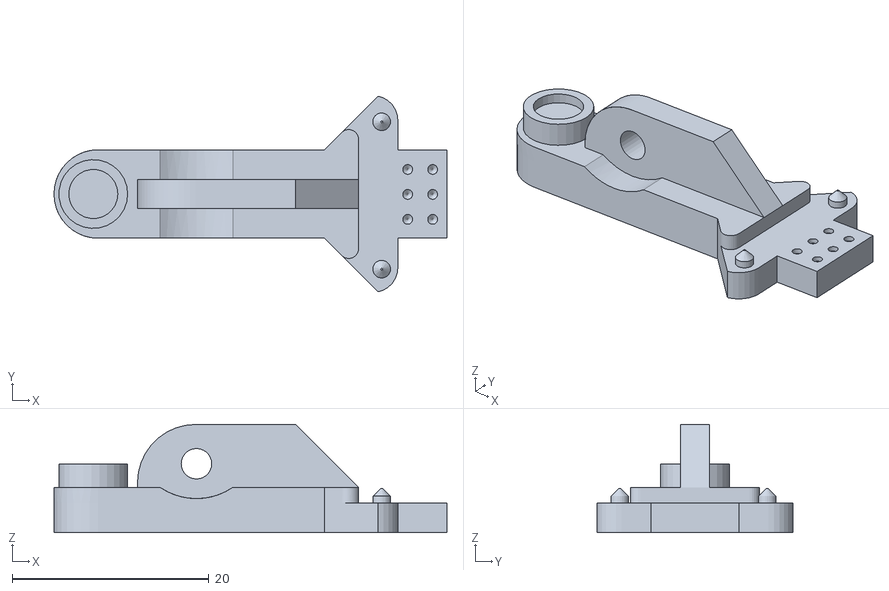
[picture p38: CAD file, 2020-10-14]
EscornaCPU/2.x/2.40/3D/Pinza_ICSP_inf.stl
40.0 x 19.9 x 11.0

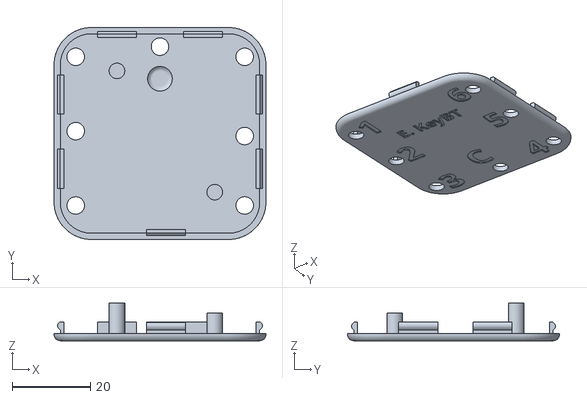
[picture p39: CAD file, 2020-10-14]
E_KEY/E_KEY_BT/3D/Tapa_E_Key_BT.stl
54.2 x 54.2 x 9.60

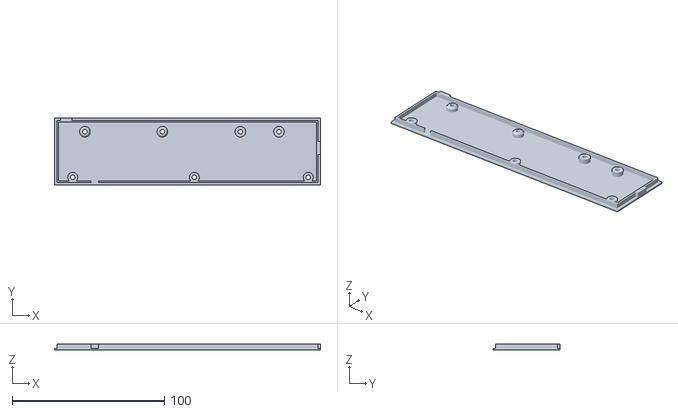
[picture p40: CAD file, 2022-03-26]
E_KEY/E_KEY_FICHA/3D/E_KEY_T_V_CaseB_6F.stl
175.0 x 44.0 x 4.00

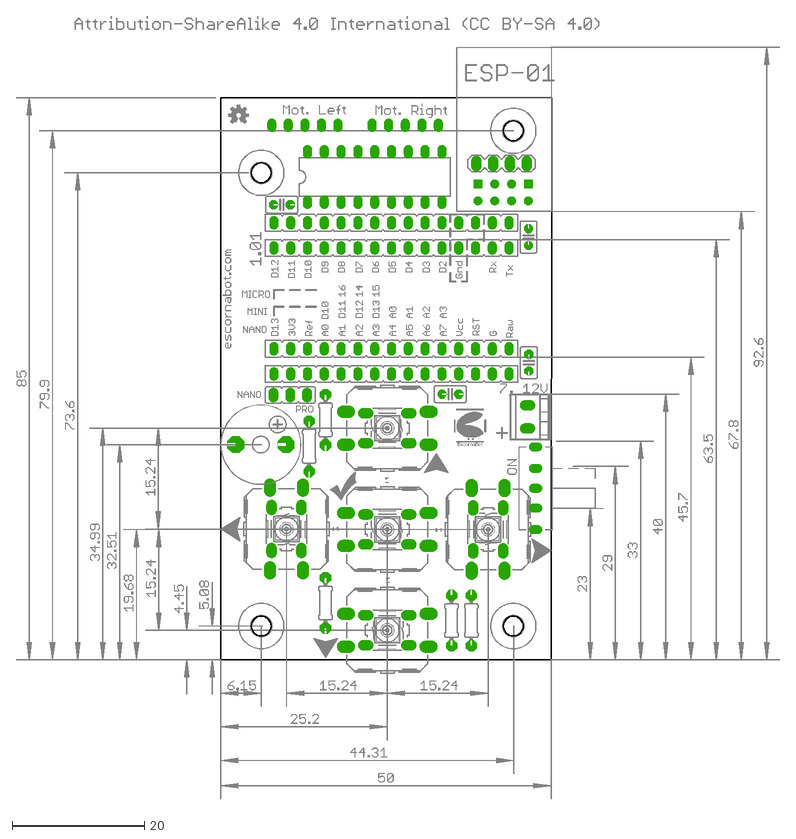
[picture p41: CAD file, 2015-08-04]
EscornaCPU/2.x/2.01/Escorna_CPU_2_01_measures.dxf
115.5 x 118.4

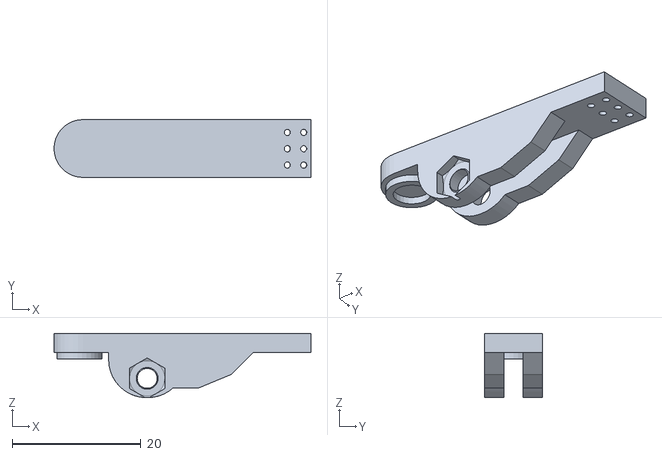
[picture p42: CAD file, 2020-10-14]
EscornaCPU/2.x/2.40/3D/Pinza_ICSP_Sup.stl
40.0 x 9.00 x 10.0

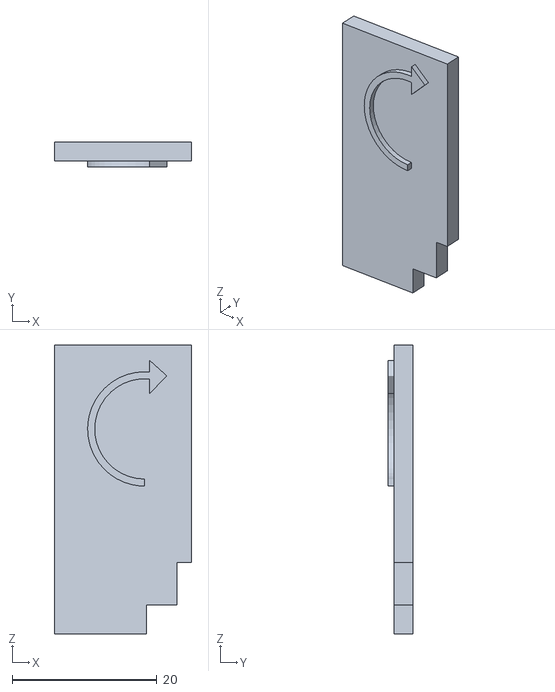
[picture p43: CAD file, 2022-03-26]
E_KEY/E_KEY_FICHA/3D/E_KEY_V_F_w.stl
19.0 x 3.45 x 40.0

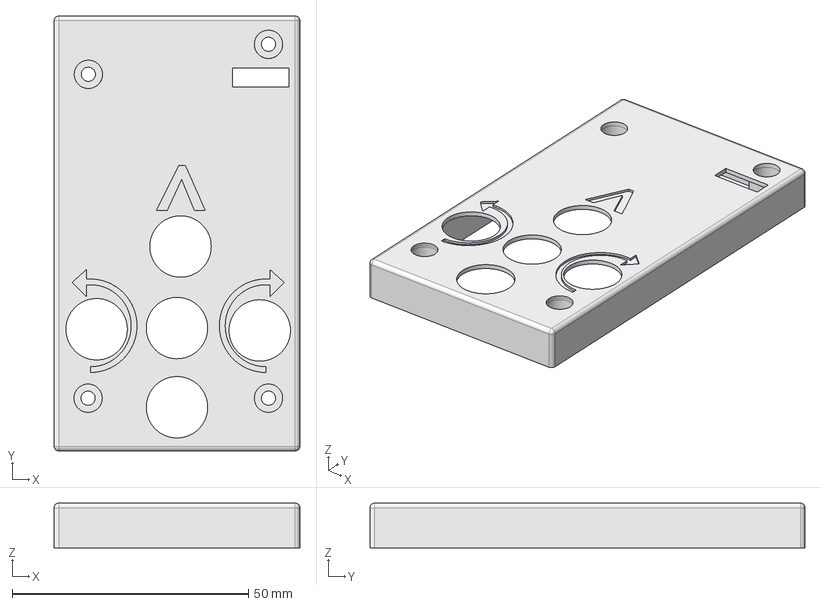
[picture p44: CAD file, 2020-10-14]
EscornaCPU/2.x/2.40/3D/Tapa_2_40.FCStd
52.0 x 92.0 x 9.50 mm

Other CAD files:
E_KEY/E_KEY_FICHA/3D/E_KEY_V_F_n.stl
E_KEY/E_KEY_FICHA/3D/E_KEY_V_F_s.stl
E_KEY/E_KEY_FICHA/3D/E_KEY_V_F_e.stl
E_KEY/E_KEY_FICHA/3D/E_KEY_T_V_6_TAB.FCStd

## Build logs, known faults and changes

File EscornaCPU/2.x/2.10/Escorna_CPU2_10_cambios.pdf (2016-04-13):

## ESCORNA CPU 2,10

Cambiase a entrada do Teclado a “A7” con pullup externo.

Todos os compoñentes poden ser:
SMD (Surface Mount Device). (https://es.wikipedia.org/wiki/Tecnolog%C3%ADa_de_montaje_superficial) ou
THT (through hole) (https://es.wikipedia.org/wiki/Tecnolog%C3%ADa_de_agujeros_pasantes)

Liña de TX en 3,3V para non fastidiar o ESP8266.

Protección contra inversión por díodo Anti-paralelo (pasante ou SMD) e PolySwitch fusible rearmable.

Cambio de posición do Interruptor,

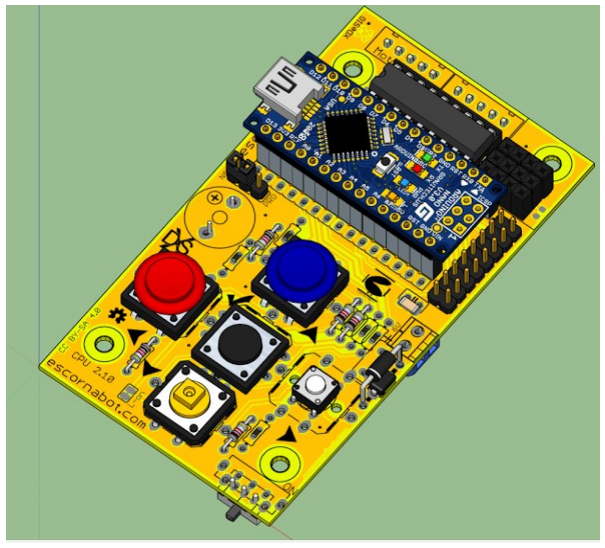
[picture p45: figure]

compatible con dous tamaños: SK-12D07 e SK-12F14

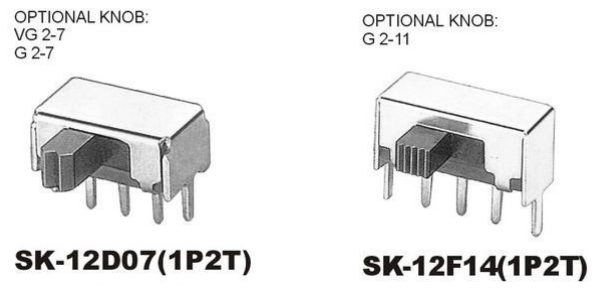
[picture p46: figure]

As teclas compatibles con Tactile Switches de 6mm 12 mm e 12mm con led (inclúe buratos de polarización)

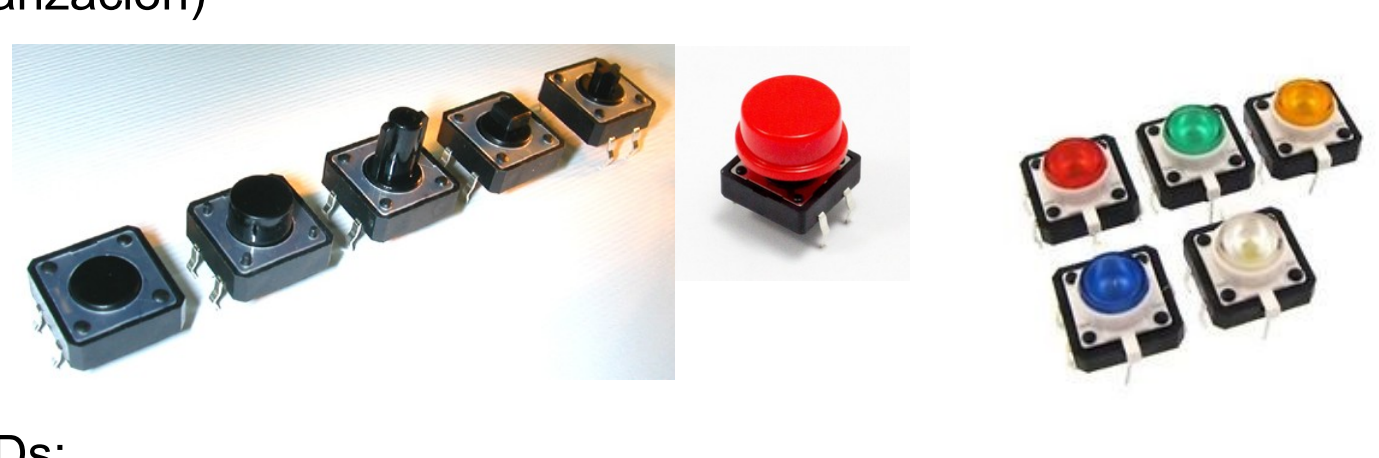
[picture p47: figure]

Asignación LEDs:

UP-A0, RIGHT-A3, DOWN-A2, LEFT-A1, GO-D13

Os leds poden desconectarse mediante o corte dunha pequena pista-Jumper, para poder utilizar esas saídas para outras cousas. (reconectanse con unha pequena soldadura), ou quitando a resistencia correspondente.

XDeSIG

Aparece o conector de expansión: dobre tira de 2,54mm

3V3 3V3
D12 D11
5V 5V
D13 A0
A1 | A2
A3 | A4
A5 | A6
GND GND

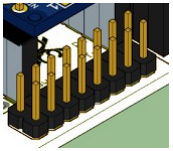
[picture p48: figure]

Eliminase un dos conectores EscornaShield (desuso).

Continua o conector SV4 (D13 – RAW) ( ampliar conexións)

O Buzer, os conectores de alimentación e motores poden conectarse por ambas caras.

Os buratos de suxeición continúan na mesma posición. (a placa ampliase 5,1mm cara atrás ).

Compatible con unha cara EscornaBot funcional (sen Leds e sinais do conector de expansión) .

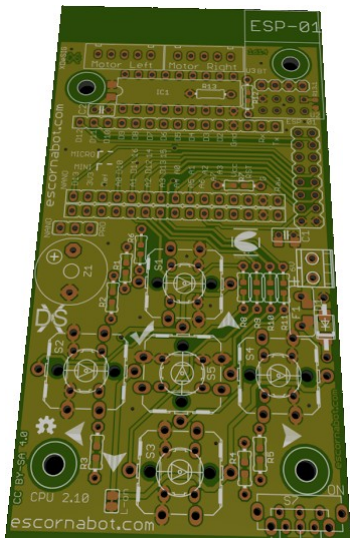
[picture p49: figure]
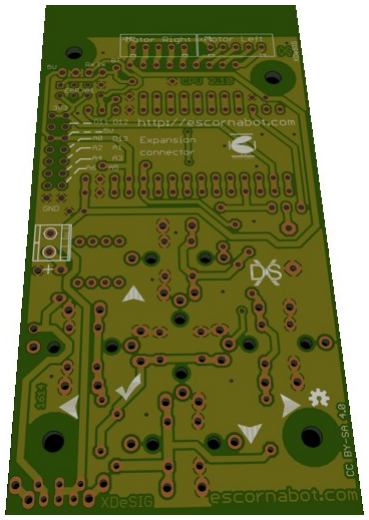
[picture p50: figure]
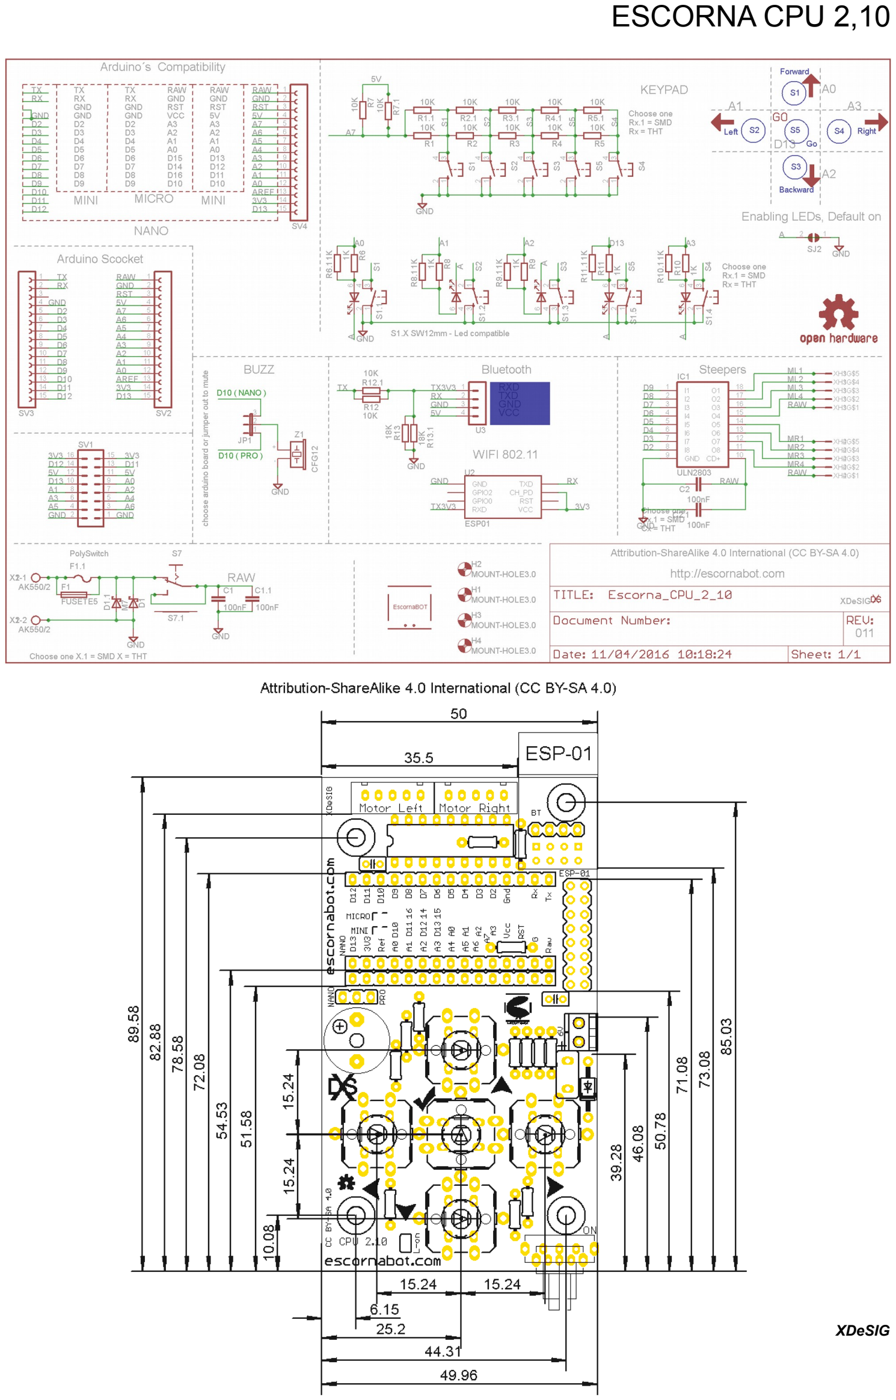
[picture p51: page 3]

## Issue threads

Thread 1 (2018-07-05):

Gerber from EscornaCPU 2.20 rejected from PCBWay.

juanmard, 2018-07-05:
Message from PCBWay:

> the copper part is too close with keepout line. Pls revise your pcb border to be bigger，the distance requires to be >=0.25mm

Explain image above.

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

In other way, file _**"escorna_cpu_2_20.kicad_pcb"**_ open in blank board with **KiCAD v4.0.7**

xdesig, 2018-07-05:
que no te vacilen

llevan hechas con ese archivo cientos de placas.

[image: image.png]

O xov., 5/07/2018 ás 21:34, Juan Manuel Rico (<notifications@github.com>)
escribiu:

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

juanmard, 2018-07-05:
Me habrá tocado el chino "chisquilloso" en PCBWay... :(
La cuestión es que he ido a modificarla y me he dado cuenta que los esquemáticos están hechos en Eagle (uso KiCAD)... pero hay un fichero PCB exportado que tampoco a KiCAD que tampoco he podido abrir. :(

¿Tienes compartida la versión 2.20 a PCBWay? :)

xdesig, 2018-07-05:
Que te parece así:
[image: image.png]

O xov., 5/07/2018 ás 21:53, Juan Manuel Rico (<notifications@github.com>)
escribiu:

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

juanmard, 2018-07-05:
No me salen tus imágenes.  :(

xdesig, 2018-07-05:
Modifico la placa para que no tengamos problemas y la subo en unos minutos.

xdesig, 2018-07-05:
Todo modificado y subido, si encuentras algún erro.. avisa
Gracias por todo

O xov., 5/07/2018 ás 22:21, Juan Manuel Rico (<notifications@github.com>)
escribiu:

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

juanmard, 2018-07-05:
De nada, gracias a ti.
Antes de que lo modificaras he hecho otro intento y ahora me lo rechazan por otra cosa.

> missing the right column line for Keep out layer.

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

Voy a volverlo a intentar con tus nuevas modificaciones.

juanmard, 2018-07-05:
No tengo suerte... con las últimas modificaciones me han enviado dos errores.

> missing the right column line for Keep out layer.

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

El fichero de KiCAD también ha desaparecido al hacer el "pull" del proyecto. :(

xdesig, 2018-07-06:
Ya lo tienes en PCBway

https://www.pcbway.com/project/shareproject/Escorna_CPU_2_20_Gerber.html

O ven., 6/07/2018 ás 00:44, Juan Manuel Rico (<notifications@github.com>)
escribiu:

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

juanmard, 2018-07-06:
Perfecto, ahora sí han dejado de quejarse. ;)
Gracias.

Closed 2018-07-06.

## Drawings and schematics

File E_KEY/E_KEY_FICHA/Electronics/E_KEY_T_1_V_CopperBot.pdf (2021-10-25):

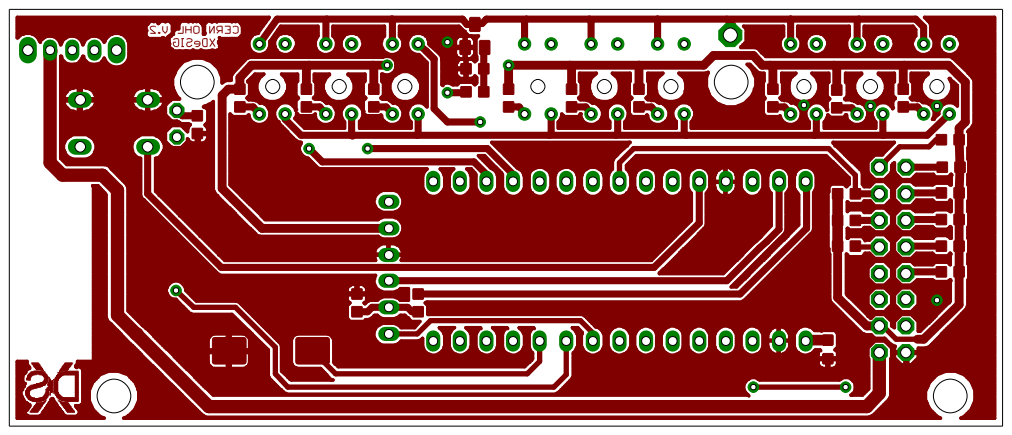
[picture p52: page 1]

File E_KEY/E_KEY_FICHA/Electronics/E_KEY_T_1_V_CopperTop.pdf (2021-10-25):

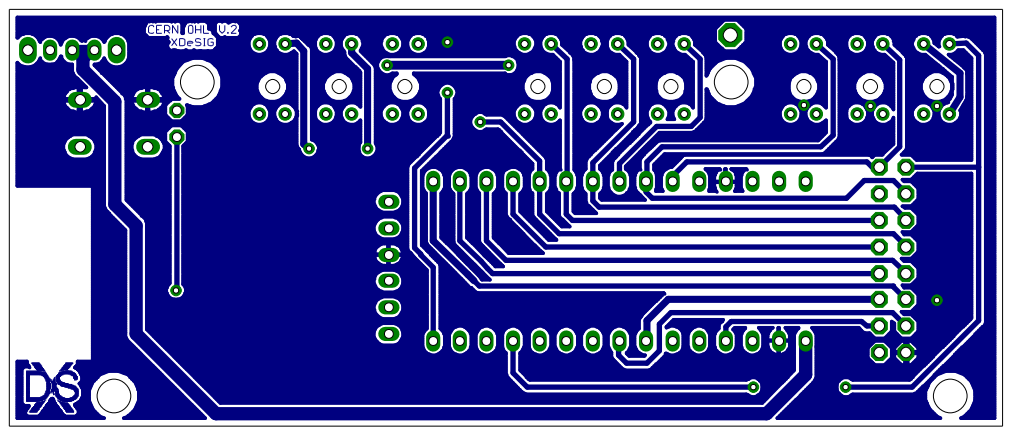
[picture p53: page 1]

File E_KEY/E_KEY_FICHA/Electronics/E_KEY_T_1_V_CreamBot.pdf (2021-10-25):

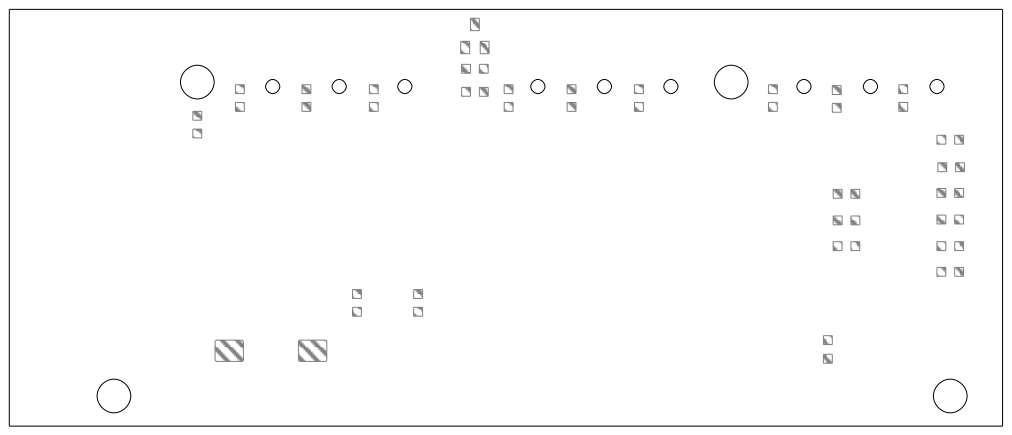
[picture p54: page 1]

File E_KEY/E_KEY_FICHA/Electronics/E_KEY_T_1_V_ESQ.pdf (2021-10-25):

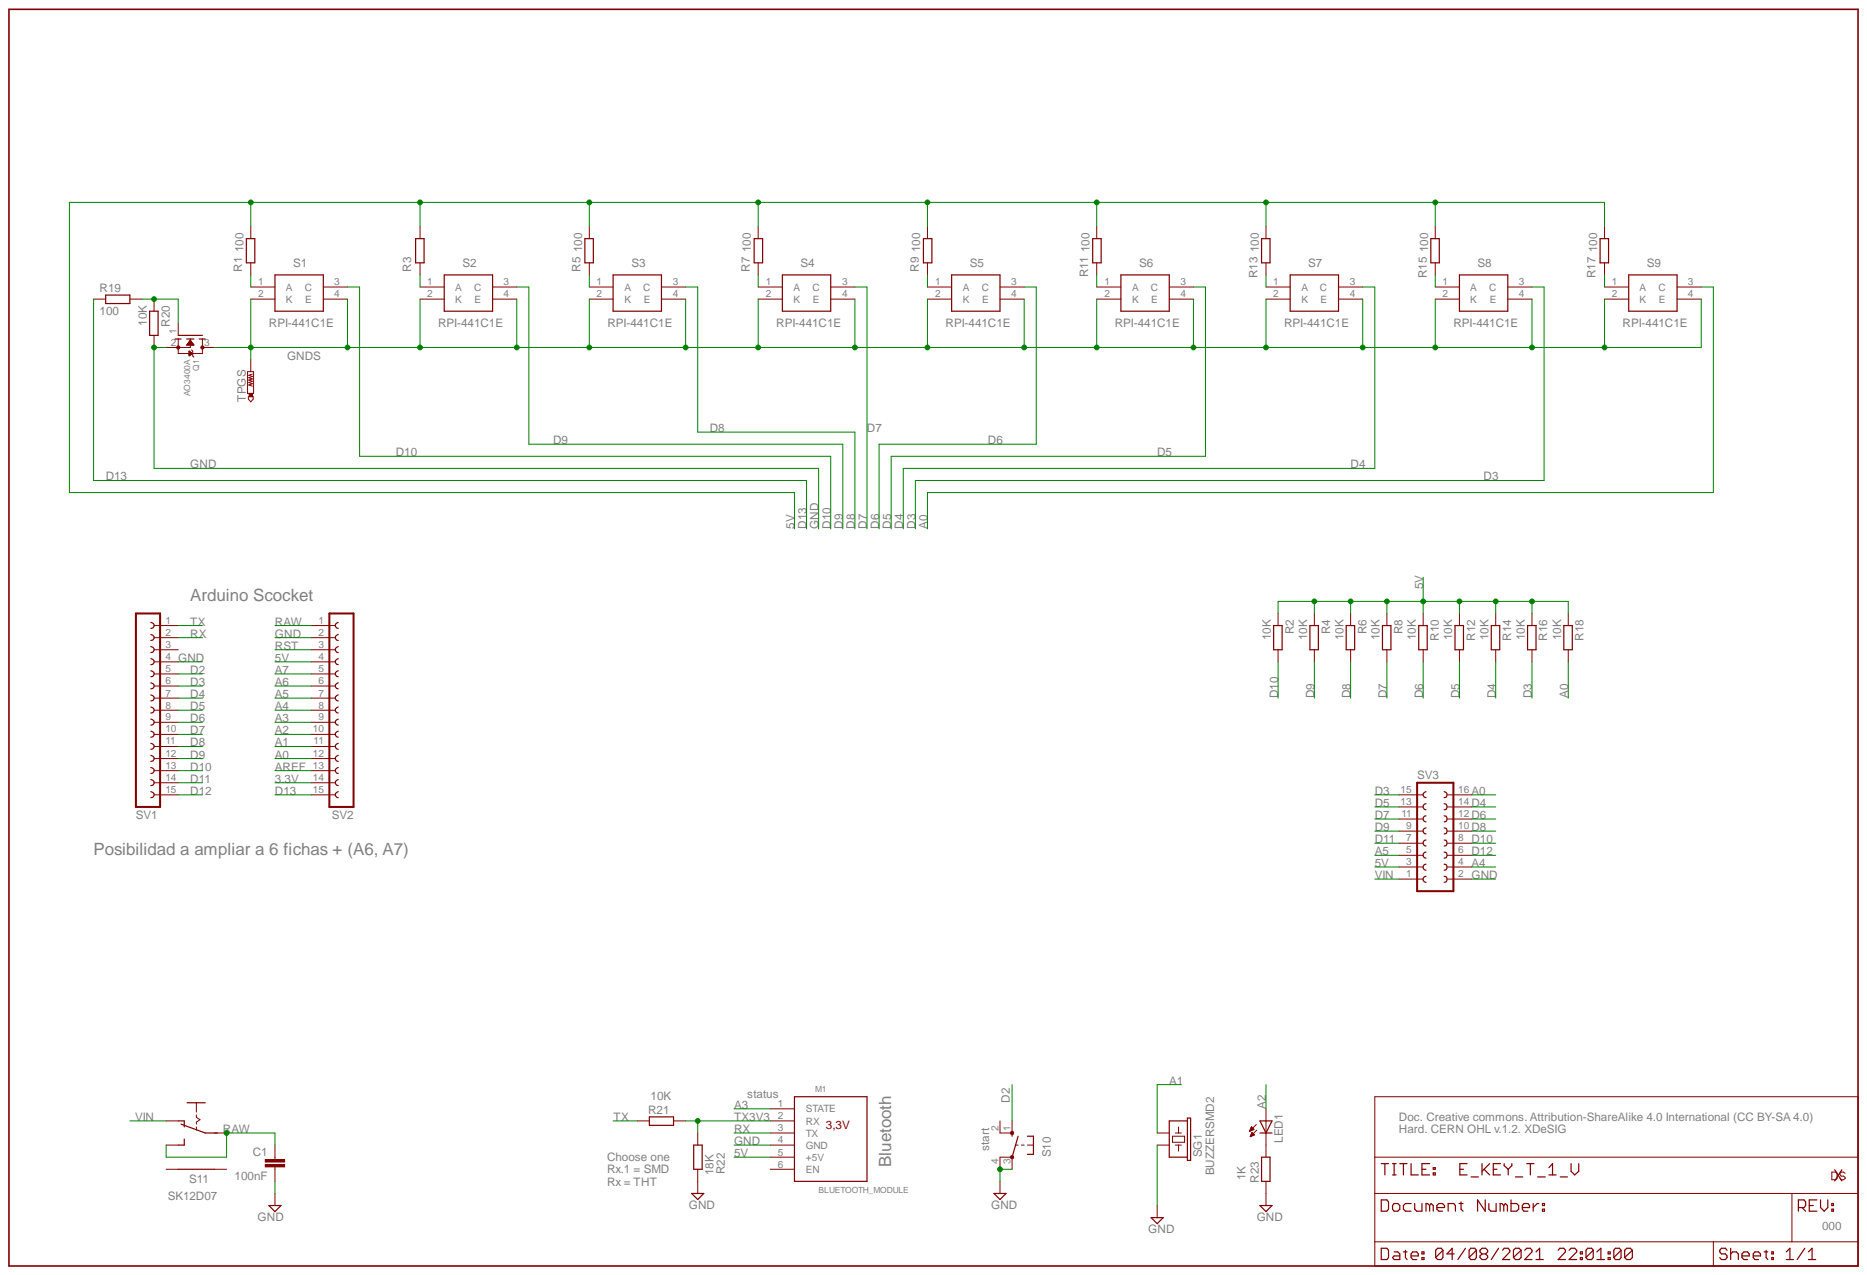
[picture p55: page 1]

Doc. Creative commons. Attribution-ShareAlike 4.0 International (CC BY-SA 4.0)
Hard. CERN OHL v.1.2. XDeSIG

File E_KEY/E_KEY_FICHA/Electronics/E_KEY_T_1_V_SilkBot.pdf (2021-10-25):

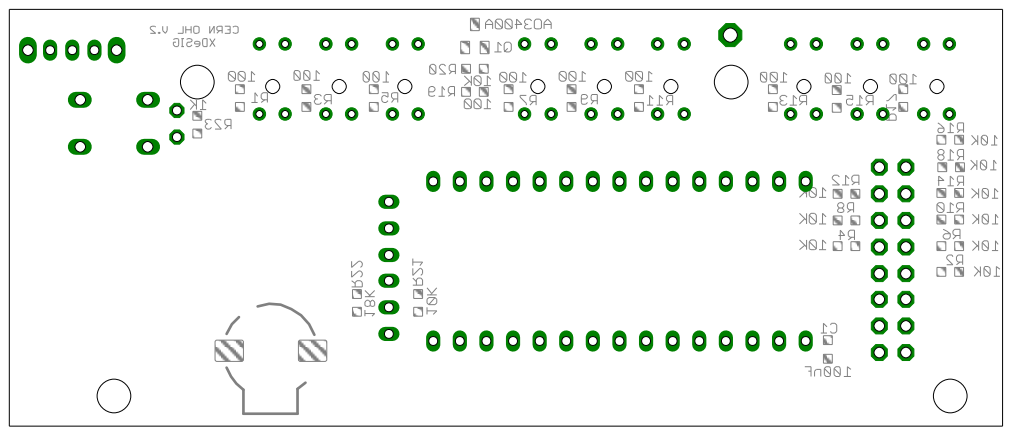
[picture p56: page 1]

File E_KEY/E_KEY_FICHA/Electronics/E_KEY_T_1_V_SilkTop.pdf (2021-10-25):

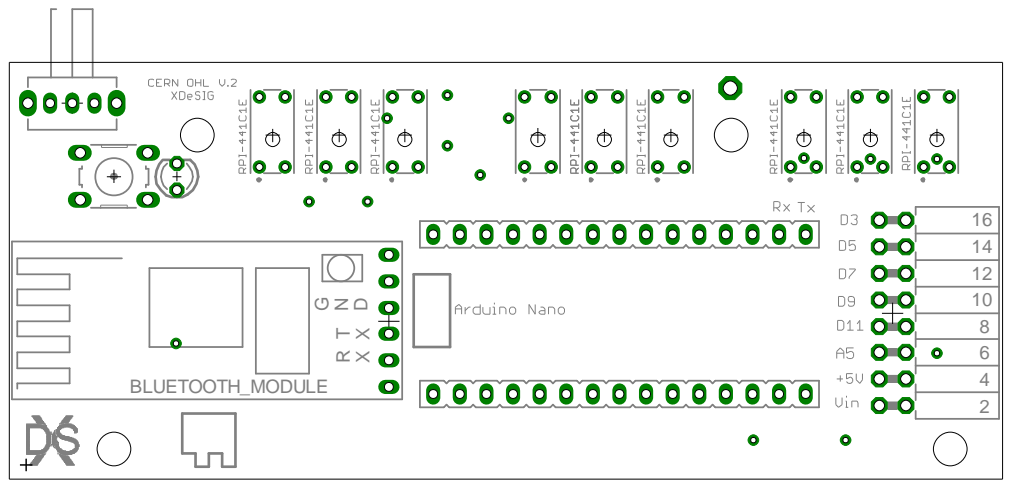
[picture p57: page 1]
BLUETOOTH_MODULE

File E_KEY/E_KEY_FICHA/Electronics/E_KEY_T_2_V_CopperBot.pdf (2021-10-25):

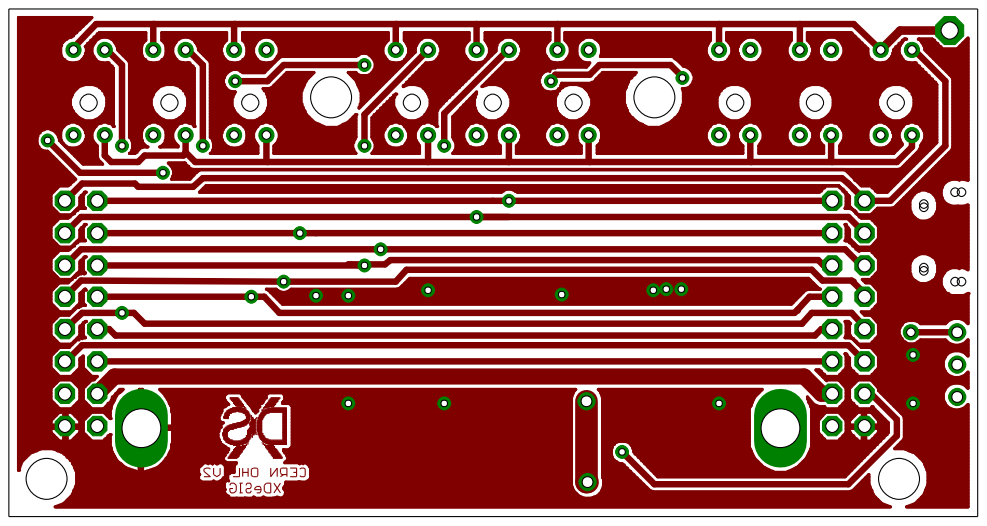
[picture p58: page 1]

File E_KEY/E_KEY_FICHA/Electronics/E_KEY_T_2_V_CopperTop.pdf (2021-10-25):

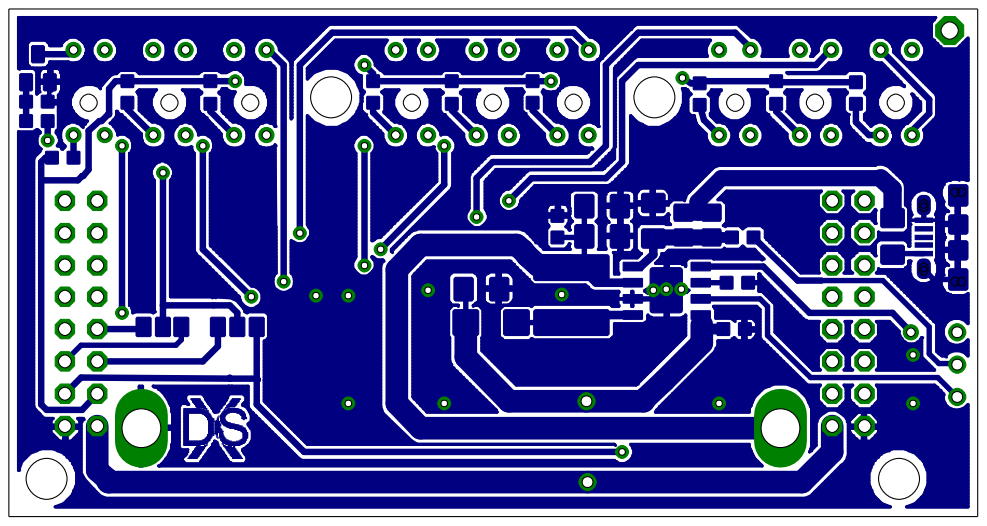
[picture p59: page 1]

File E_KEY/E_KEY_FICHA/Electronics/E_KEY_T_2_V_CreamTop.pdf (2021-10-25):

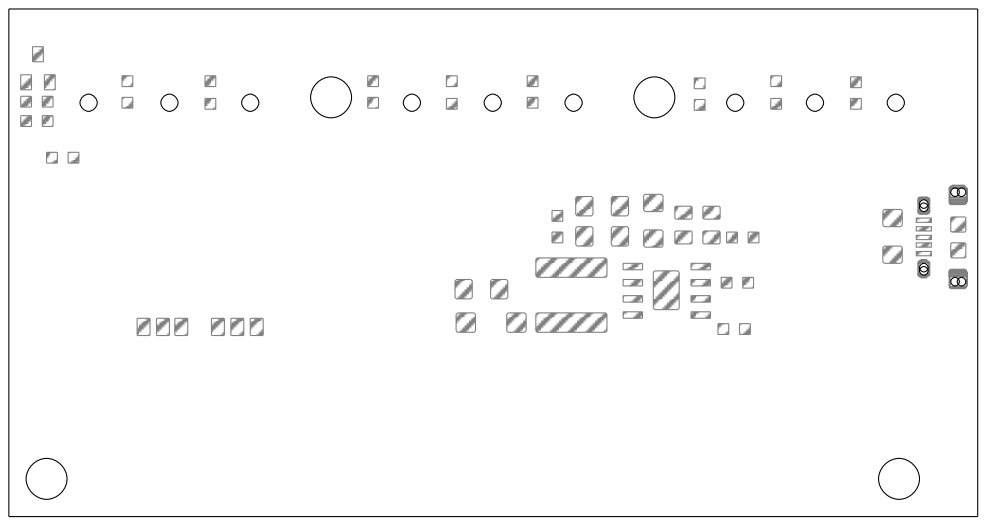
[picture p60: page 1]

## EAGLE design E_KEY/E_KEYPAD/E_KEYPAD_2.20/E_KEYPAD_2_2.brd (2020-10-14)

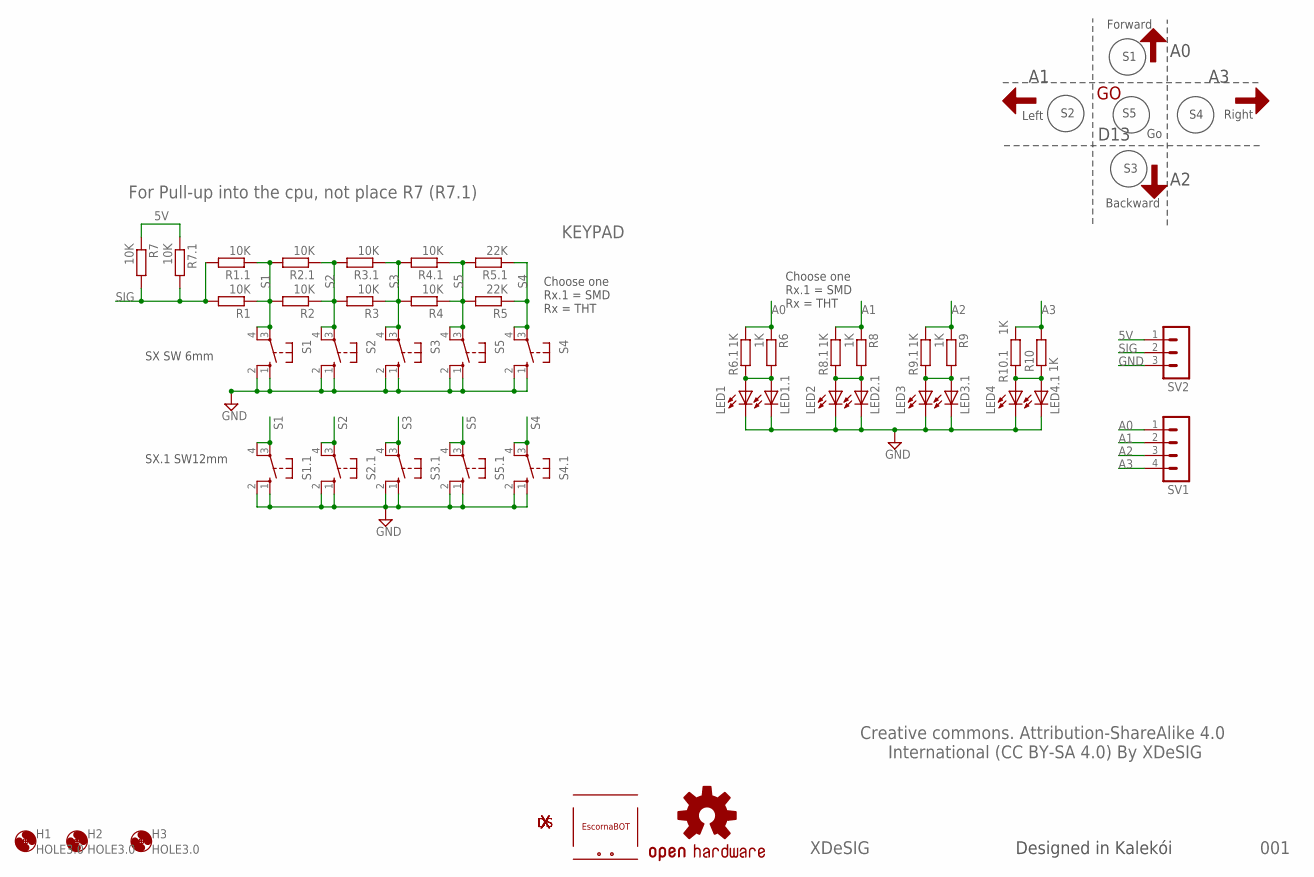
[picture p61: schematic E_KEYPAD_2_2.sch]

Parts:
H1, H2, H3: HOLE3.0; 3,0
LED1, LED2, LED3, LED4: LED3MM
LED1.1, LED2.1, LED3.1, LED4.1: LEDCHIPLED_0603; CHIPLED_0603
LOGO2: OSHW-LOGOS; OSHW-LOGO-S
R1, R2, R3, R4, R7: 10K; 0204/7
R1.1, R2.1, R3.1, R4.1, R7.1: 10K; R0603
R5: 22K; 0204/7
R5.1: 22K; R0603
R6, R8, R9, R10: 1K; 0204/7
R6.1, R8.1, R9.1, R10.1: 1K; R0603
S1, S2, S3, S4, S5: 10-XX; B3F-10XX
S1.1, S2.1, S3.1, S4.1, S5.1: 40-XX; B3F-40XX
SV1: MA04-1
SV2: MA03-1
U$1: ESCORNABOT; ESCORNA_PEQUE
U$3, U$4, U$6, U$11: FRECHA
U$5: GO; VALE
U$7: XDESIG21; XDESIG
U$10: XDESIG; XDESIG_CU_2

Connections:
5V: R7.1, R7.1.1, SV2.1
A0: R6.1, R6.1.1, SV1.1
A1: R8.1, R8.1.1, SV1.2
A2: R9.1, R9.1.1, SV1.3
A3: R10.2, R10.1.1, SV1.4
GND: LED1.K (C), LED1.1.C, LED2.K (C), LED2.1.C, LED3.K (C), LED3.1.C, LED4.K (C), LED4.1.C, S1.1 (S), S1.2 (S1), S1.1.1 (S), S1.1.2 (S1), S2.1 (S), S2.2 (S1), S2.1.1 (S), S2.1.2 (S1), S3.1 (S), S3.2 (S1), S3.1.1 (S), S3.1.2 (S1), S4.1 (S), S4.2 (S1), S4.1.1 (S), S4.1.2 (S1), S5.1 (S), S5.2 (S1), S5.1.1 (S), S5.1.2 (S1), SV2.3
unnamed: LED2.A, LED2.1.A, R8.2, R8.1.2
unnamed: LED1.A, LED1.1.A, R6.2, R6.1.2
unnamed: LED3.A, LED3.1.A, R9.2, R9.1.2
unnamed: LED4.A, LED4.1.A, R10.1, R10.1.2
S1: R1.1, R1.1.1, R2.2, R2.1.2, S1.3, S1.4 (P1), S1.1.3, S1.1.4 (P1)
S2: R2.1, R2.1.1, R3.2, R3.1.2, S2.3, S2.4 (P1), S2.1.3, S2.1.4 (P1)
S3: R3.1, R3.1.1, R4.2, R4.1.2, S3.3, S3.4 (P1), S3.1.3, S3.1.4 (P1)
S4: R5.1, R5.1.1, S4.3, S4.4 (P1), S4.1.3, S4.1.4 (P1)
S5: R4.1, R4.1.1, R5.2, R5.1.2, S5.3, S5.4 (P1), S5.1.3, S5.1.4 (P1)
SIG: R1.2, R1.1.2, R7.2, R7.1.2, SV2.2

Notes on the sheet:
For Pull-up into the cpu, not place R7 (R7.1)
001
Creative commons. Attribution-ShareAlike 4.0 International (CC BY-SA 4.0) By XDeSIG
XDeSIG
KEYPAD
Choose one Rx.1 = SMD Rx = THT
SX.1 SW12mm
SX SW 6mm
Forward
Left
Right
Backward
D13
Designed in Kalekói

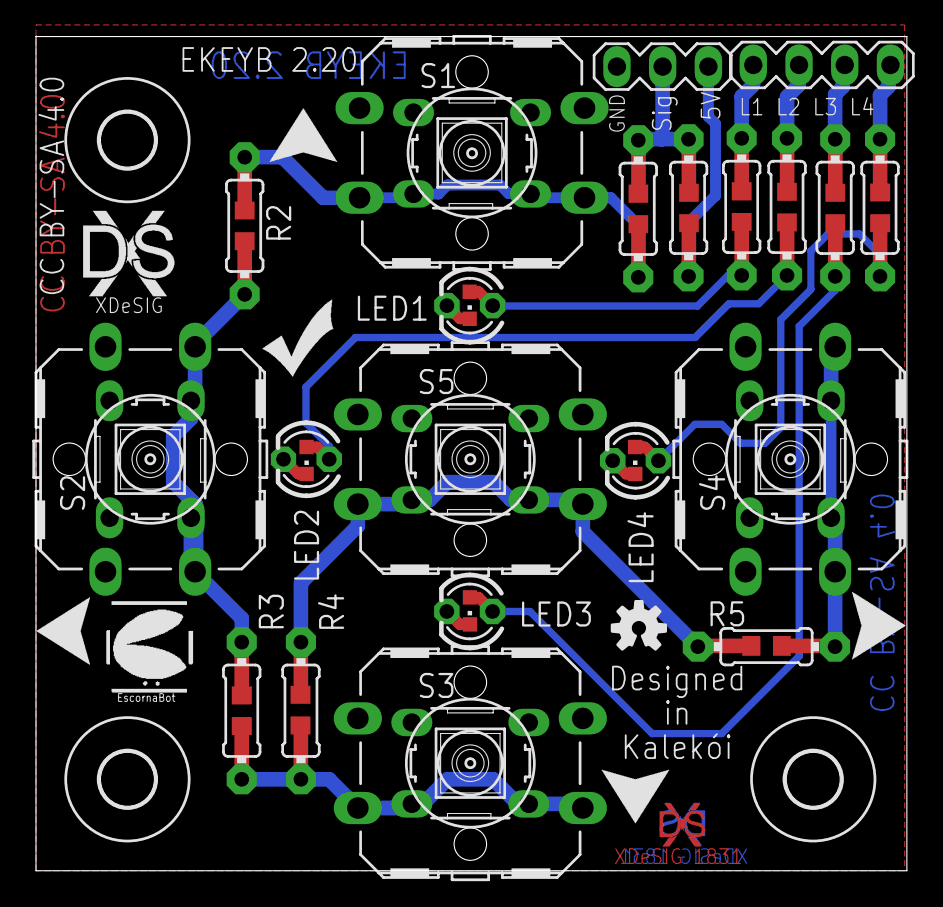
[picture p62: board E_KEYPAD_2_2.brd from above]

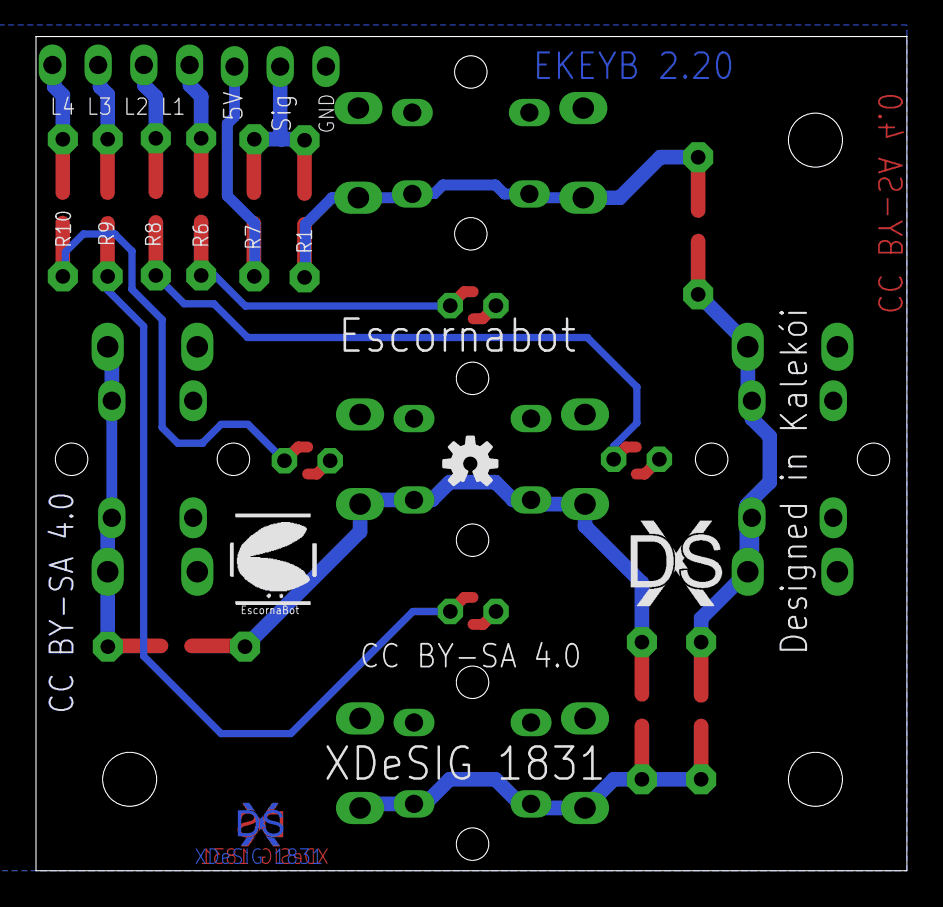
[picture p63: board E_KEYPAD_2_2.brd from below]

Board: 2 copper layers, 48.4 x 46.4 mm, 56 parts (4 on the bottom side), 16 nets.

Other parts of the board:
LOGO1: OSHW-LOGOS; OSHW-LOGO-S
U$2: ESCORNABOT; ESCORNA_PEQUE
U$8: XDESIG; XDESIG_CU_2
U$9: XDESIG21; XDESIG

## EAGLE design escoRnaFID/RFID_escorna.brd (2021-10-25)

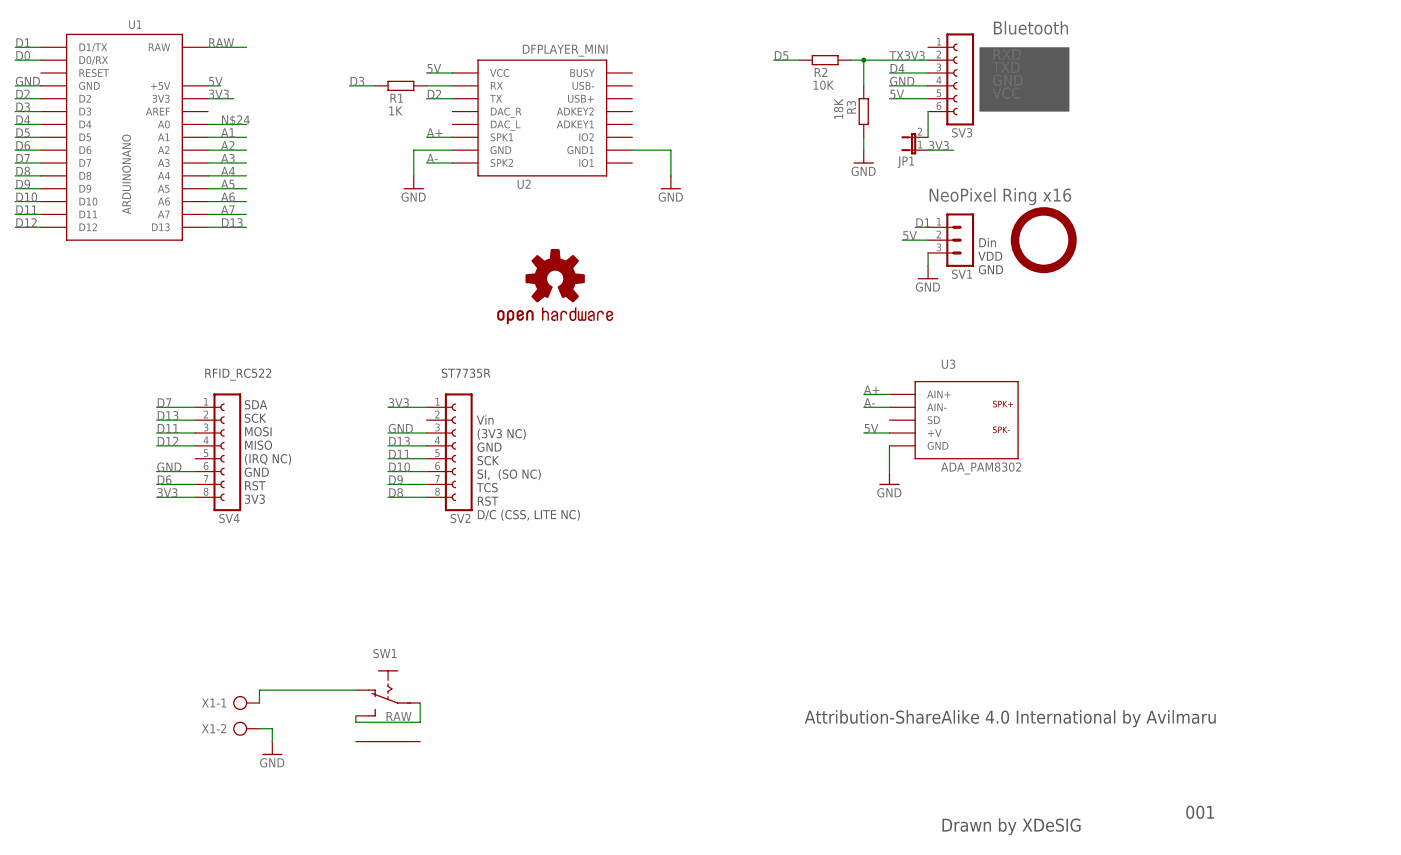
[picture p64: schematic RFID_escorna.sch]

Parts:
JP1: JUMPER_JP1E; JUMPER_JP1
LOGO1: OSHW-LOGOS; ESCORNA_LBRESCORNA_CPU_2_10_SPARKFUN-AESTHETICS_OSHW-LOGO-S
R1: 1K; 0204/7
R2: 10K; 0204/7
R3: 18K; 0204/7
SV1: MA03-1
SV2, SV4: FE08-1; FE08
SV3: FE06-1; FE06
SW1: ESCORNA_ELIB_ESCORNA_SK12F14D; ESCORNA_ELIB_ESCORNA_SK-12D07
U1: ARDUINONANO; ARDUINO_NANO_NO_ICSP
U2: DFPLAYER_MINI; DFR0299
U3: ADA_PAM8302; ADA_PAM8320
X1: AK500/2

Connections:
3V3: JP1.1, SV2.1, SV4.8, U1.3V3
5V: SV1.2, SV3.5, U1.5V (+5V), U2.P$1 (VCC), U3.P$2 (+V)
A1: U1.A1
A2: U1.A2
A3: U1.A3
A4: U1.A4
A5: U1.A5
A6: U1.A6
A7: U1.A7
A+: U2.P$6 (SPK1), U3.P$5 (AIN+)
A-: U2.P$8 (SPK2), U3.P$4 (AIN-)
D0: U1.D0/RX
D1: SV1.1, U1.D1/TX
D2: U1.D2, U2.P$3 (TX)
D3: R1.1, U1.D3
D4: SV3.3, U1.D4
D5: R2.1, U1.D5
D6: SV4.7, U1.D6
D7: SV4.1, U1.D7
D8: SV2.8, U1.D8
D9: SV2.7, U1.D9
D10: SV2.6, U1.D10
D11: SV2.5, SV4.3, U1.D11
D12: SV4.4, U1.D12
D13: SV2.4, SV4.2, U1.D13
GND: R3.2, SV1.3, SV2.3, SV3.4, SV4.6, U1.GND, U1.GND1 (GND), U2.P$7 (GND), U2.P$10 (GND1), U3.P$1 (GND), X1.2
unnamed: JP1.2, SV3.6
unnamed: SW1.P$2 (O), X1.1
unnamed: R1.2, U2.P$2 (RX)
RAW: SW1.P$1, SW1.P$3 (S), U1.RAW
TX3V3: R2.2, R3.1, SV3.2

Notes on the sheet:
Bluetooth
RXD
TXD
GND
VCC
NeoPixel Ring x16
RFID_RC522
SDA SCK MOSI MISO (IRQ NC) GND RST 3V3
ST7735R
Vin (3V3 NC) GND SCK SI, (SO NC) TCS RST D/C (CSS, LITE NC)
001
Din VDD GND
Attribution-ShareAlike 4.0 International by Avilmaru
Drawn by XDeSIG

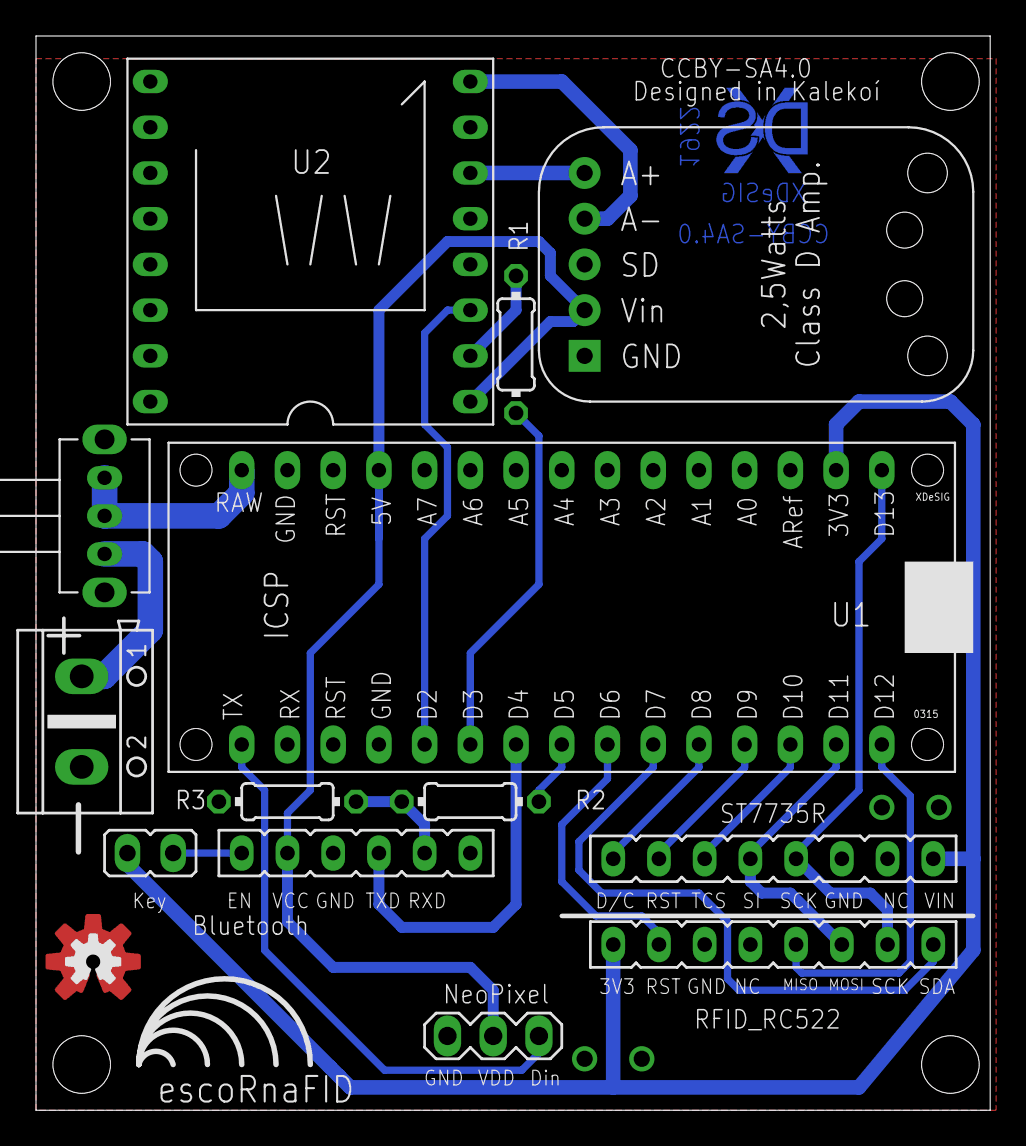
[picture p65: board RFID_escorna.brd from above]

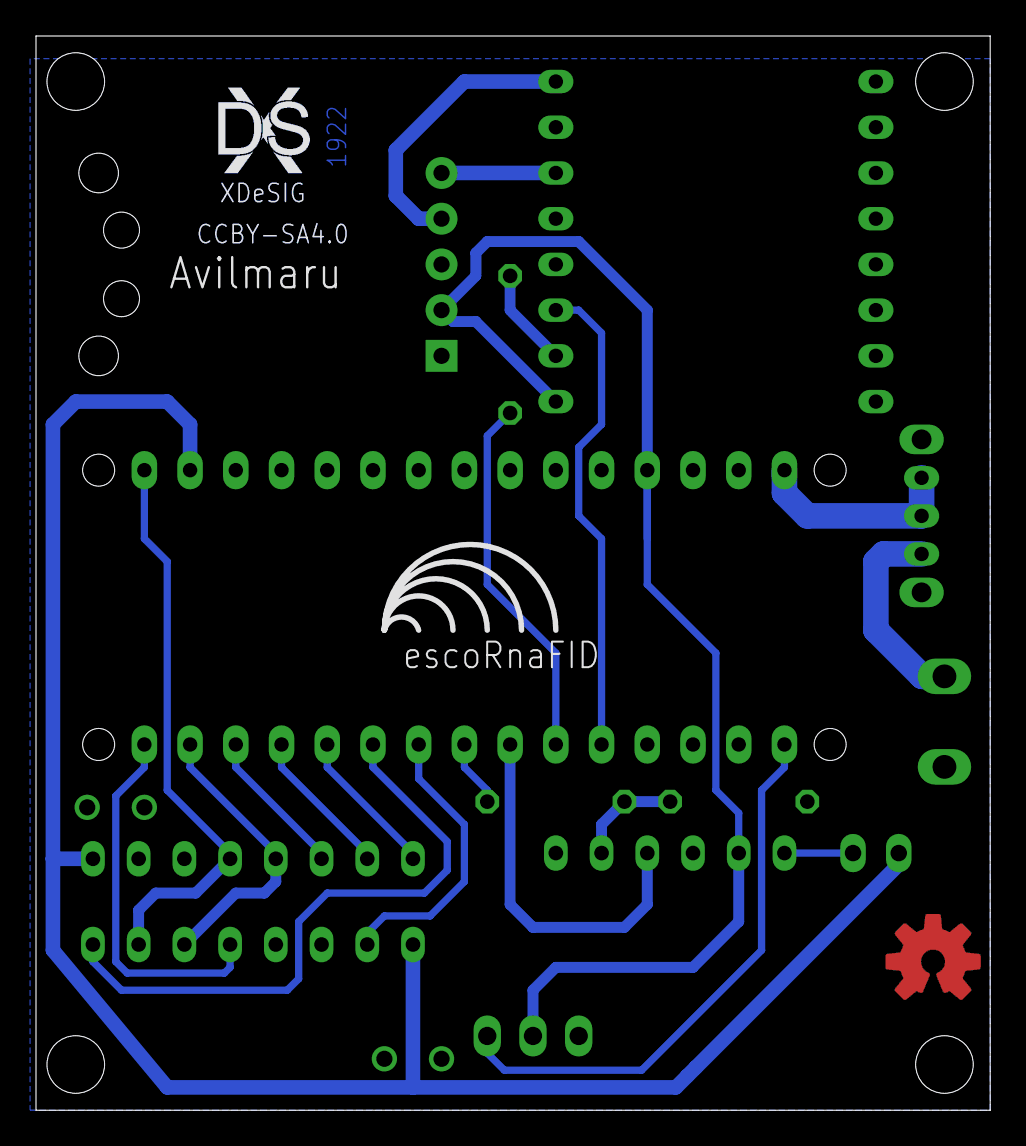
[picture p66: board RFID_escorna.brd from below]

Board: 2 copper layers, 53.0 x 59.7 mm, 17 parts (2 on the bottom side), 23 nets.

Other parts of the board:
U$1: XDESIG_CU
U$2: OSHWLOGO_TOP_0.2
U$5: XDESIG

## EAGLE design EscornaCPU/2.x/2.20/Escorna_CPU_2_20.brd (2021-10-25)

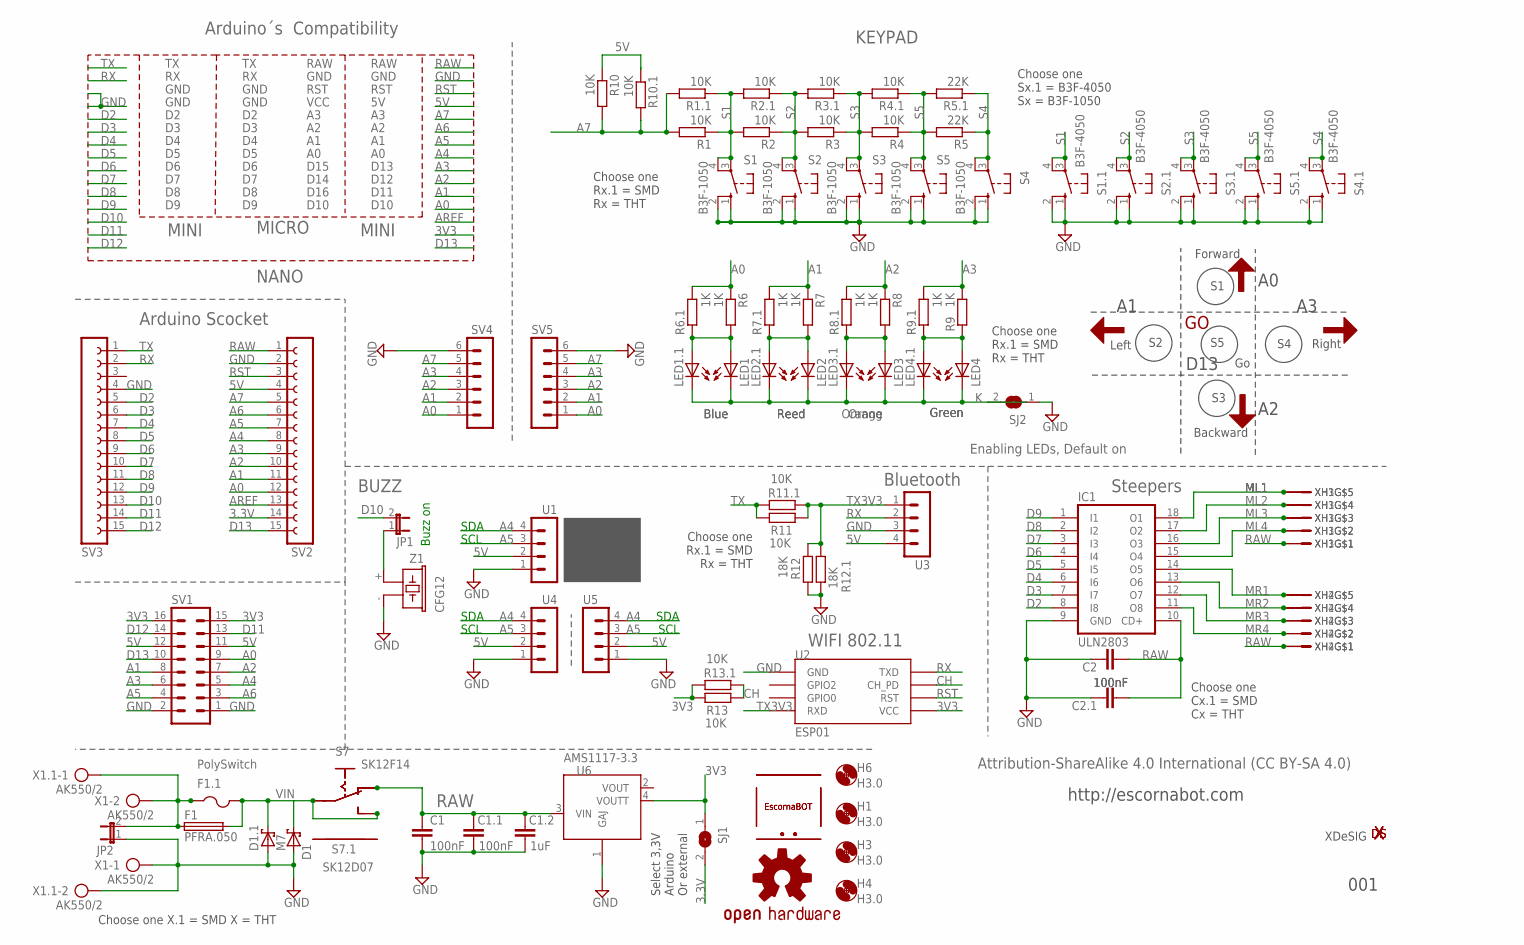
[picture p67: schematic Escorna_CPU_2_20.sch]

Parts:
C1, C2: 100nF; C025-025X050
C1.1, C2.1: 100nF; C0603K
C1.2: 1uF; C0603K
D1: 1N5817; DO41-10
D1.1: M7; SMA
ESC1, ESC2: ESCORNABOT; ESCORNA_PEQUE
F1: PFRA.050; TE5
F1.1: PolySwitch; R1206
H1, H3, H4, H6: H3.0; 3,0
IC1: ULN2803; DIL18
JP1, JP2: JP1E; 1X02
LED1: Blue; LED3MM
LED1.1: Blue; CHIPLED_0603
LED2: Reed; LED3MM
LED2.1: Reed; CHIPLED_0603
LED3: Orange; LED3MM
LED3.1: Orang; CHIPLED_0603
LED4: Green; LED3MM
LED4.1: Green; CHIPLED_0603
LOGO2: OSHW-LOGOS; OSHW-LOGO-S
R1, R2, R3, R4, R10, R11, R13: 10K; 0204/7
R1.1, R2.1, R3.1, R4.1, R10.1, R11.1, R13.1: 10K; R0603
R5: 22K; 0204/7
R5.1: 22K; R0603
R6, R7, R8, R9: 1K; 0204/7
R6.1, R7.1, R8.1, R9.1: 1K; R0603
R12: 18K; 0204/7
R12.1: 18K; R0603
S1, S2, S3, S4, S5: B3F-1050; B3F-10XX
S1.1, S2.1, S3.1, S4.1, S5.1: B3F-4050; B3F-40XX
S7: SK12F14; ESCORNA_SK-12F14-G
S7.1: SK12D07; ESCORNA_SK-12D07
SJ1, SJ2: SJ
SV1: MA08-2
SV2, SV3: 1x15 SOCKET STRIP; CON-LSTA_FE15
SV4, SV5: MA06-1
U1, U3, U4, U5: MA04-1
U2: ESP01
U6: AMS1117-3.3; SOT223
U$1, U$3, U$6, U$11: FRECHA
U$2: GO; VALE
U$13: XDESIG_XDESIG21; XDESIG_XDESIG
X1, X1.1: AK550/2
XDS1: XDESIG; XDESIG_CU_2
XH1, XH2, XH3, XH4: B5B-XH-A
Z1: CFG12; F/CM12P

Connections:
3.3V: SJ1.2, SV2.14
3V3: R13.1, R13.1.1, SJ1.1, SV1.15, SV1.16, U2.VCC, U6.4 (VOUTT)
5V: R10.1, R10.1.1, SV1.11, SV1.12, SV2.4, U1.2, U3.4, U4.2, U5.2
A0: R6.1, R6.1.1, SV1.9, SV2.12, SV4.1, SV5.1
A1: R7.1, R7.1.1, SV1.8, SV2.11, SV4.2, SV5.2
A2: R8.1, R8.1.1, SV1.7, SV2.10, SV4.3, SV5.3
A3: R9.2, R9.1.1, SV1.6, SV2.9, SV4.4, SV5.4
A4: SV1.5, SV2.8, U1.4, U4.4, U5.4
A5: SV1.4, SV2.7, U1.3, U4.3, U5.3
A6: SV1.3, SV2.6
A7: R1.2, R1.1.2, R10.2, R10.1.2, SV2.5, SV4.5, SV5.5
AREF: SV2.13
CH: R13.2, R13.1.2, U2.CH_PD
D2: IC1.8 (I8), SV3.5
D3: IC1.7 (I7), SV3.6
D4: IC1.6 (I6), SV3.7
D5: IC1.5 (I5), SV3.8
D6: IC1.4 (I4), SV3.9
D7: IC1.3 (I3), SV3.10
D8: IC1.2 (I2), SV3.11
D9: IC1.1 (I1), SV3.12
D10: JP1.2, SV3.13
D11: SV1.13, SV3.14
D12: SV1.14, SV3.15
D13: SV1.10, SV2.15
GND: C1.2, C1.1.1, C1.2.1, C2.1, C2.1.1, D1.A, D1.1.A, IC1.9 (GND), JP2.1, R12.2, R12.1.1, S1.1 (S), S1.2 (S1), S1.1.1 (S), S1.1.2 (S1), S2.1 (S), S2.2 (S1), S2.1.1 (S), S2.1.2 (S1), S3.1 (S), S3.2 (S1), S3.1.1 (S), S3.1.2 (S1), S4.1 (S), S4.2 (S1), S4.1.1 (S), S4.1.2 (S1), S5.1 (S), S5.2 (S1), S5.1.1 (S), S5.1.2 (S1), SJ2.1, SV1.1, SV1.2, SV2.2, SV3.4, SV4.6, SV5.6, U1.1, U2.GND, U3.3, U4.1, U5.1, U6.1 (GAJ), X1.1, X1.1.2, Z1.- (2)
K: LED1.K (C), LED1.1.C, LED2.K (C), LED2.1.C, LED3.K (C), LED3.1.C, LED4.K (C), LED4.1.C, SJ2.2
ML1: IC1.18 (O1), XH1.P$5, XH3.P$5
ML2: IC1.17 (O2), XH1.P$4, XH3.P$4
ML3: IC1.16 (O3), XH1.P$3, XH3.P$3
ML4: IC1.15 (O4), XH1.P$2, XH3.P$2
MR1: IC1.14 (O5), XH2.P$5, XH4.P$5
MR2: IC1.13 (O6), XH2.P$4, XH4.P$4
MR3: IC1.12 (O7), XH2.P$3, XH4.P$3
MR4: IC1.11 (O8), XH2.P$2, XH4.P$2
unnamed: JP1.1, Z1.+ (1)
unnamed: F1.1, F1.1.1, JP2.2, X1.2, X1.1.1
unnamed: LED2.A, LED2.1.A, R7.2, R7.1.2
unnamed: LED1.A, LED1.1.A, R6.2, R6.1.2
unnamed: LED3.A, LED3.1.A, R8.2, R8.1.2
unnamed: LED4.A, LED4.1.A, R9.1, R9.1.2
unnamed: S7.P$4, S7.1.P$4
unnamed: S7.P$5, S7.1.P$5
RAW: C1.1, C1.1.2, C1.2.2, C2.2, C2.1.2, IC1.10 (CD+), S7.P$2 (O), S7.1.P$2 (O), SV2.1, U6.3 (VIN), XH1.P$1, XH2.P$1, XH3.P$1, XH4.P$1
RST: SV2.3, U2.RST
RX: SV3.2, U2.TX (TXD), U3.2
S1: R1.1, R1.1.1, R2.2, R2.1.2, S1.3, S1.4 (P1), S1.1.3, S1.1.4 (P1)
S2: R2.1, R2.1.1, R3.2, R3.1.2, S2.3, S2.4 (P1), S2.1.3, S2.1.4 (P1)
S3: R3.1, R3.1.1, R4.2, R4.1.2, S3.3, S3.4 (P1), S3.1.3, S3.1.4 (P1)
S4: R5.1, R5.1.1, S4.3, S4.4 (P1), S4.1.3, S4.1.4 (P1)
S5: R4.1, R4.1.1, R5.2, R5.1.2, S5.3, S5.4 (P1), S5.1.3, S5.1.4 (P1)
TX: R11.1, R11.1.1, SV3.1
TX3V3: R11.2, R11.1.2, R12.1, R12.1.2, U2.RX (RXD), U3.1
VIN: D1.C, D1.1.C, F1.2, F1.1.2, S7.P$1, S7.P$3 (S), S7.1.P$1, S7.1.P$3 (S)

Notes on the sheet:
Arduino Scocket
Steepers
KEYPAD
BUZZ
Bluetooth
Buzz on
NANO
Arduino´s Compatibility
MINI
MICRO
GND
RAW
RST
VCC
D13
D15
D12
D14
D11
D16
D10
Attribution-ShareAlike 4.0 International (CC BY-SA 4.0)
Forward
Left
Right
Backward
WIFI 802.11
Choose one Rx.1 = SMD Rx = THT
Choose one X.1 = SMD X = THT
XDeSIG
http://escornabot.com
Choose one Cx.1 = SMD Cx = THT
001
Enabling LEDs, Default on
SCL
SDA
Choose one Sx.1 = B3F-4050 Sx = B3F-1050
Select 3,3V Arduino Or external

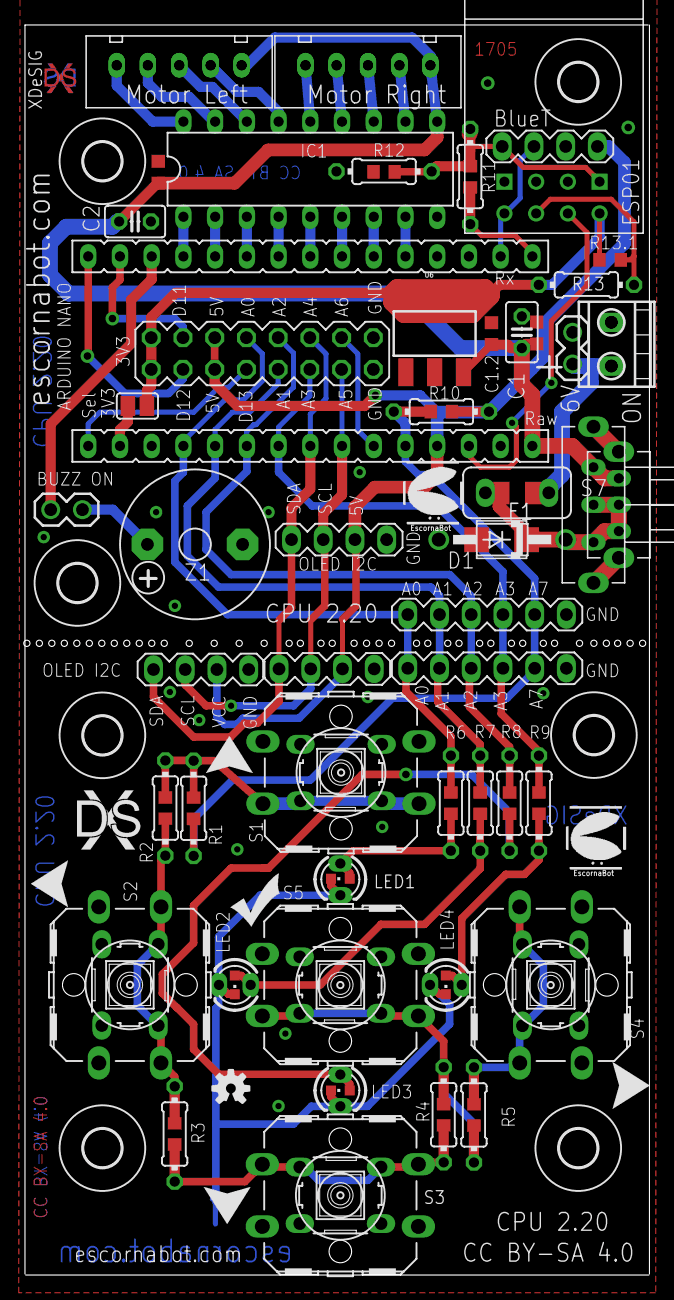
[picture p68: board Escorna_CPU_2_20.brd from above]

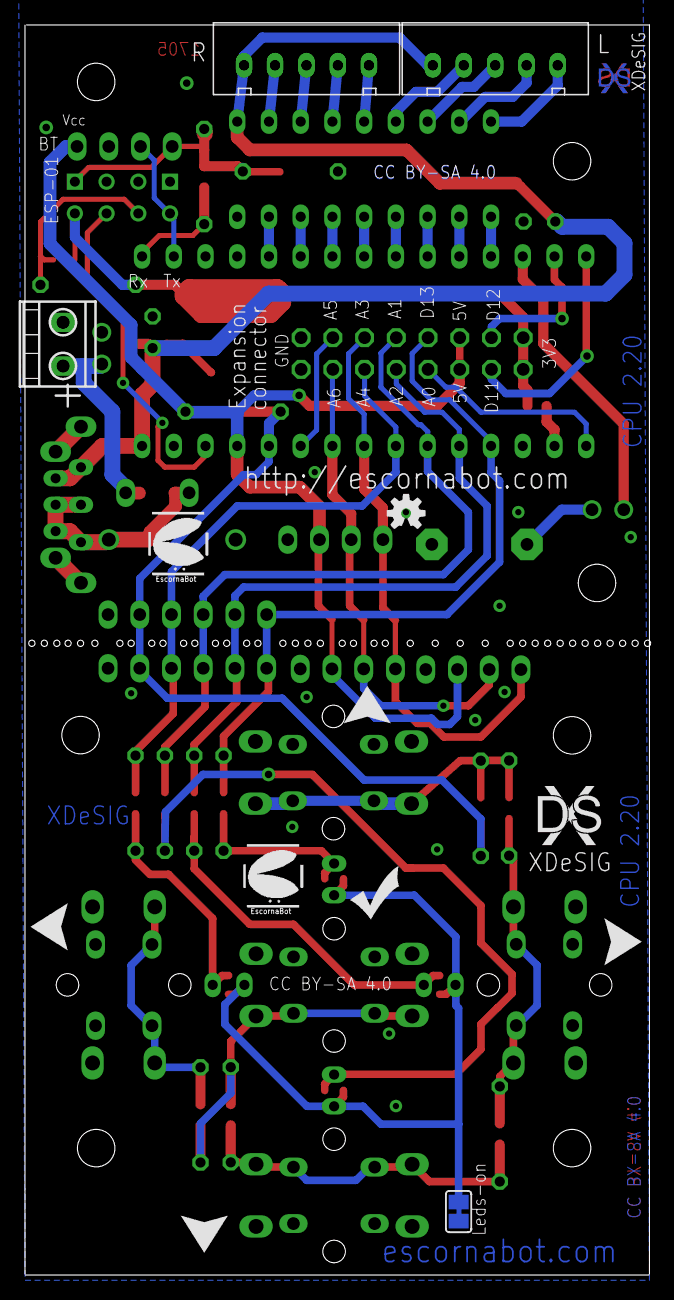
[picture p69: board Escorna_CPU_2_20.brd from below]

Board: 2 copper layers, 50.0 x 100.1 mm, 105 parts (14 on the bottom side), 53 nets.

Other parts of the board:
ESC: ESCORNABOT; ESCORNA_PEQUE
H2, H5, H7: MOUNT-HOLE3.0; 3,0
LOGO1: OSHW-LOGOS; OSHW-LOGO-S
U$4, U$7, U$8, U$9: FRECHA
U$5: ESCORNABOT; ESCORNA_PEQUE
U$10: GO; VALE
U$12: XDESIG_XDESIG21; XDESIG_XDESIG
XDS: XDESIG; XDESIG_CU_2

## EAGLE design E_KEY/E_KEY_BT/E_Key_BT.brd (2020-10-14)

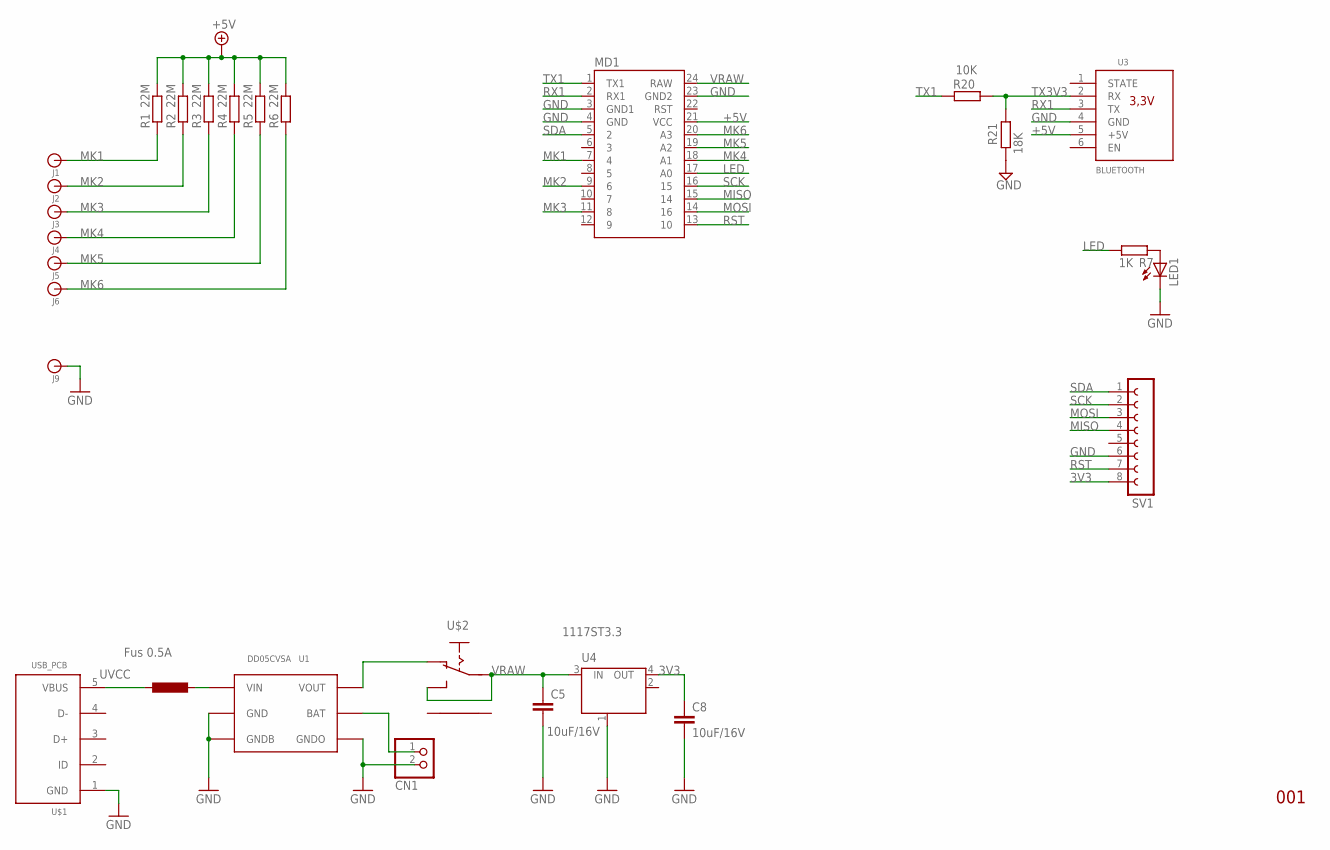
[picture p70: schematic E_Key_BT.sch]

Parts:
C5, C8: 10uF/16V; C1206
CN1: JST_2PIN-THM-RA; JST-PH-2-THM-RA
F1: Fus 0.5A; R1206
J1, J2, J3, J4, J5, J6, J9: Hole; BANANA_CONN
LED1: LED3MM
MD1: PRO_MICRO
R1, R2, R3, R4, R5, R6: 22M; R0603
R7: 1K; R0603
R20: 10K; R0603
R21: 18K; R0603
SV1: FE08-1; FE08
U1: DD05CVSA
U3: BLUETOOTH; BLUETOOTH_MODULE
U4: 1117ST3.3; SOT223
U$1: USB_PCB
U$2: ESCORNA_SK12F14D; ESCORNA_SK-12D07

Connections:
3V3: C8.1, SV1.8, U4.4 (OUT)
+5V: MD1.21 (VCC), R1.2, R2.2, R3.2, R4.2, R5.2, R6.2, U3.5 (+5V)
GND: C5.2, C8.2, CN1.2 (1), J9.P$1, LED1.K (C), MD1.3 (GND1), MD1.4 (GND), MD1.23 (GND2), R21.1, SV1.6, U1.P$2 (GND), U1.P$4 (GNDB), U1.P$5 (GNDO), U3.4 (GND), U4.1 (GND/ADJ), U$1.1 (GND)
LED: MD1.17 (A0), R7.2
MISO: MD1.15 (14), SV1.4
MK1: J1.P$1, MD1.7 (4), R1.1
MK2: J2.P$1, MD1.9 (6), R2.1
MK3: J3.P$1, MD1.11 (8), R3.1
MK4: J4.P$1, MD1.18 (A1), R4.1
MK5: J5.P$1, MD1.19 (A2), R5.1
MK6: J6.P$1, MD1.20 (A3), R6.1
MOSI: MD1.14 (16), SV1.3
unnamed: U1.P$6 (VOUT), U$2.P$2 (O)
unnamed: LED1.A, R7.1
unnamed: F1.1, U1.P$1 (VIN)
unnamed: CN1.1 (2), U1.P$3 (BAT)
RST: MD1.13 (10), SV1.7
RX1: MD1.2 (RX1), U3.3 (TX)
SCK: MD1.16 (15), SV1.2
SDA: MD1.5 (2), SV1.1
TX1: MD1.1 (TX1), R20.1
TX3V3: R20.2, R21.2, U3.2 (RX)
UVCC: F1.2, U$1.5 (VBUS)
VRAW: C5.1, MD1.24 (RAW), U4.3 (IN), U$2.P$1, U$2.P$3 (S)

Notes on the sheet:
001

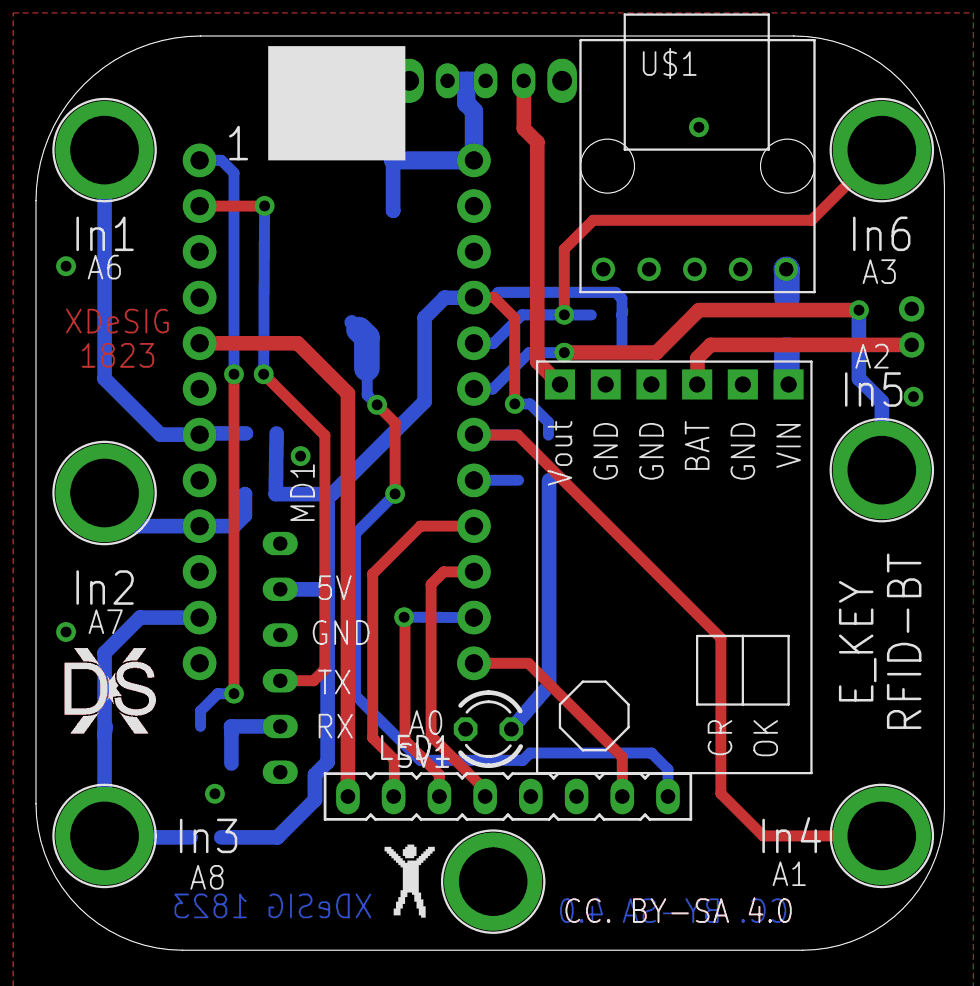
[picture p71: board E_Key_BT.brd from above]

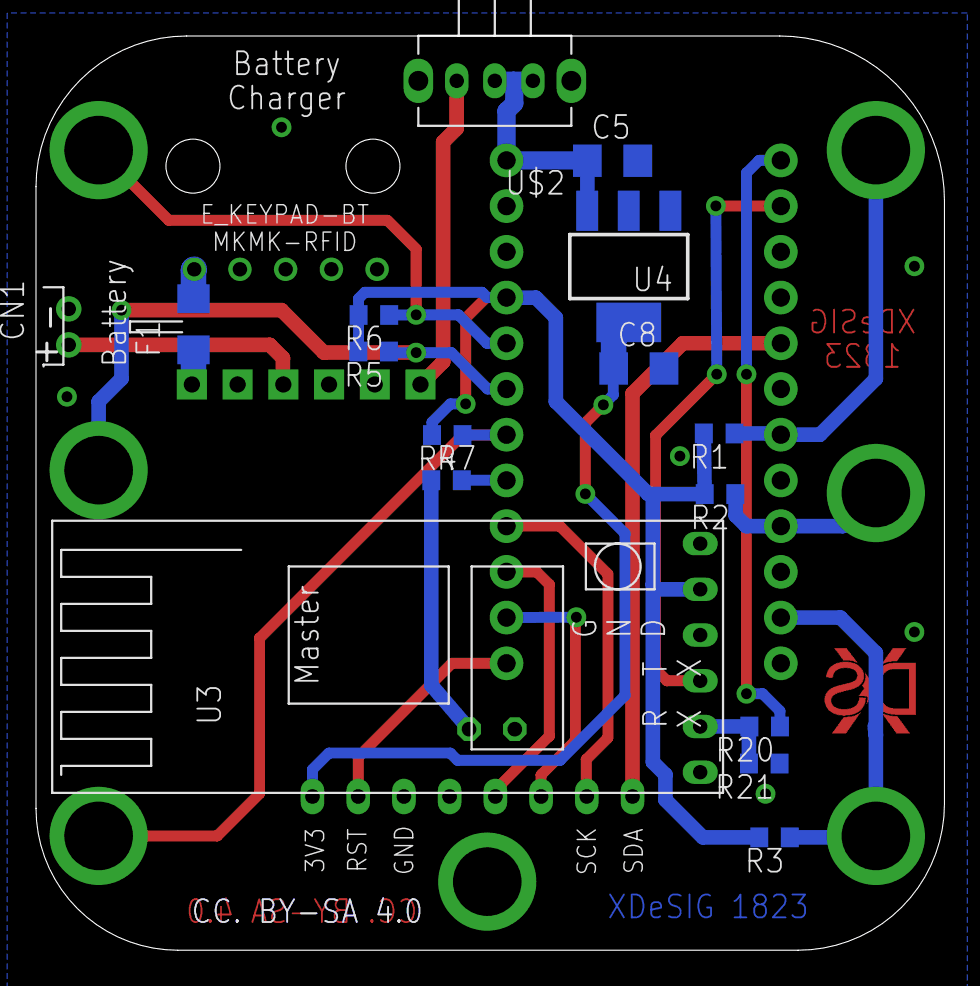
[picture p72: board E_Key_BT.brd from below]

Board: 2 copper layers, 50.5 x 50.8 mm, 31 parts (16 on the bottom side), 24 nets.

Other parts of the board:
U$3: XDESIG_CU
U$4: BODY
U$5: XDESIG

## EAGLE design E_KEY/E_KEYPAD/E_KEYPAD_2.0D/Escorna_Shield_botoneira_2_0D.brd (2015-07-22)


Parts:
ESSH1: OUTL_ESCORNASHILED; OUTL_ESCORNASHIELD
J1: FE13-1; FE13
J2, J4: 22-05-7028-02; 7395-02
J3: 22-05-7038-03; 7395-03
LED5MM: LED5MM
LOGO2: OSHW-LOGOS; OSHW-LOGO-S
RT.1, RT.2, RT.3, RT.4, RT.5, RT.6: 10K; 0204/7
RT.7: 1K; 0204/7
S1, S2, S3, S4, S5, S6: B3F-40XX; B3F40XX_NH
S7: 10-XX; B3F-10XX
SJ1: SOLDERJUMPER_2WAY; SJ_2
U$1: ESCORNABOT; ESCORNA_PEQUE
U$3: XDESIG21; XDESIG
U$4, U$5, U$6, U$7: FRECHA
U$8: GO; VALE
U$9: CANCELA; ASPA
U$10: XDESIG; XDESIG_CU_2

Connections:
3V3: ESSH1.3V3 (3V3N), J1.11
A0: ESSH1.A0 (A0_D10_D10), J1.9
A1: ESSH1.A1 (A1_D11_D16), J1.8
A2: ESSH1.A2 (A2_D12_D14), J1.7
A3: ESSH1.A3 (A3_D13_D15), J1.6
A4: ESSH1.A4 (KEY/A4_A0_A0), J2.2, J4.2, RT.1.2
A6: ESSH1.A6 (A6_A2_A2), J1.3
A7: ESSH1.A7 (A7_A3_A3), J1.2
AREF: ESSH1.AREF (AREFN), J1.10
D11: ESSH1.D11 (D11N), J3.1
D12: ESSH1.D12 (D12N), J3.2
D13: ESSH1.D13 (D13N), J1.12
GND: ESSH1.GND, ESSH1.GND1, ESSH1.GND2, J1.13, J2.1, J3.3, J4.1, LED5MM.K (C), S1.1 (S), S1.2 (S1), S2.1 (S), S2.2 (S1), S3.1 (S), S3.2 (S1), S4.1 (S), S4.2 (S1), S5.1 (S), S5.2 (S1), S6.1 (S), S6.2 (S1), S7.1 (S), S7.2 (S1)
LED_PL: ESSH1.A5 (A5_A1_A1), RT.7.2
unnamed: LED5MM.A, RT.7.1
unnamed: J1.1, SJ1.2
unnamed: RT.2.2, S1.4 (P1)
unnamed: RT.1.1, S1.3
unnamed: RT.5.2, S4.4 (P1)
unnamed: RT.6.1, S6.3, S6.4 (P1)
unnamed: RT.4.1, S4.3
unnamed: RT.3.1, RT.4.2, S3.3
unnamed: RT.2.1, S2.3
unnamed: RT.3.2, S2.4 (P1)
unnamed: RT.5.1, RT.6.2, S5.4 (P1)
RAW: ESSH1.RAW (VIN_RAW), SJ1.1
RST: ESSH1.RST, S7.3
VCC: ESSH1.VCC, SJ1.3

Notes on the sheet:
Shield Botoneira con Pull-up no Arduino
000.D
XDeSIG
Forward
Left
Right
Backward
Clear
Led en placa
A1_D11_D16
A2_D12_D14
A3_D13_D15
Voltage Selector for J1 connector
Reset
Led on board
Keypad
Escornabot CPU1.0 connector
Connector to other CPUs
Aux. Connectors
Nano
Mini
Micro pro
90º rotate
Creative Commons Attribution-ShareAlike 4.0 International (CC BY-SA 4.0)



Board: 2 copper layers, 50.2 x 50.2 mm, 33 parts (8 on the bottom side), 28 nets.

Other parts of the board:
LOGO1: OSHW-LOGOS; OSHW-LOGO-S
U$2: ESCORNABOT; ESCORNA_PEQUE

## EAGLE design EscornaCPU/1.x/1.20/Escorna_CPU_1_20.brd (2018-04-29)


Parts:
C1, C3: 100nF; C025-025X050
C1.1, C3.1: 100nF; C0603K
C2: 1uF; C1206K
D1: 1N5817; DO41-10
D1.1: M7; SMA-DO214AC
ESC1, ESC2: ESCORNABOT; ESCORNA_PEQUE
F1: PFRA.050; TE5
F1.1: PolySwitch; R1206
H3, H4: H3.0; 3,0
IC1: ULN2803; DIL18
JP1, JP2: JP1E; 1X02
JP3, JP4: JP1E; JP1
JP5: JP4E; JP4
LOGO2: OSHW-LOGOS; OSHW-LOGO-S
R1, R2, R4, R5: 10K; 0204/7
R1.1, R2.1, R4.1, R5.1: 10K; R0603
R3: 18K; 0204/7
R3.1: 18K; R0603
S7: SK12F14; ESCORNA_SK-12F14-G
S7.1: SK12D07; ESCORNA_SK-12D07
SJ1: SJ
SV1, SV2: 1x15 SOCKET STRIP; CON-LSTA_FE15
SV3, SV4, SV5, SV6: MA06-1
U2: ESP01
U3: MA04-1
U6: 1117-3.3; SOT223
U$1, U$13: XDESIG_XDESIG21; XDESIG_XDESIG
X1, X1.1: AK550/2
XDS1: XDESIG; XDESIG_CU_2
XH1, XH2, XH3, XH4: B5B-XH-A
Z1: CFG12; F/CM12P

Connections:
3.3V: SJ1.2, SV2.14
3V3: R4.1, R4.1.1, R5.1, R5.1.1, SJ1.1, U2.VCC, U6.4 (VOUTT)
5V: JP3.1, JP3.2, JP5.3, R1.1, R1.1.1, SV2.4, SV4.1, SV4.2, SV4.3, SV4.4, SV4.5, SV4.6, U3.4
A0: SV2.12, SV6.1
A1: SV2.11, SV6.2
A2: SV2.10, SV6.3
A3: SV2.9, SV6.4
A4: JP5.1, SV2.8, SV3.1
A5: JP5.2, SV2.7, SV3.2
A6: SV2.6, SV3.3
A7: R1.2, R1.1.2, SV2.5, SV6.5
AREF: SV2.13
CH: R4.2, R4.1.2, U2.GPIO0
D2: IC1.8 (I8), SV1.5
D3: IC1.7 (I7), SV1.6
D4: IC1.6 (I6), SV1.7
D5: IC1.5 (I5), SV1.8
D6: IC1.4 (I4), SV1.9
D7: IC1.3 (I3), SV1.10
D8: IC1.2 (I2), SV1.11
D9: IC1.1 (I1), SV1.12
D10: JP1.2, SV1.13
D11: SV1.14, SV3.4
D12: SV1.15, SV3.5
D13: SV2.15, SV3.6
GND: C1.2, C1.1.1, C2.1, C3.1, C3.1.1, D1.A, D1.1.A, IC1.9 (GND), JP2.1, JP4.1, JP4.2, JP5.4, R3.2, R3.1.1, SV1.4, SV2.2, SV5.1, SV5.2, SV5.3, SV5.4, SV5.5, SV5.6, SV6.6, U2.GND, U3.3, U6.1 (GAJ), X1.1, X1.1.2, Z1.- (2)
ML1: IC1.18 (O1), XH1.P$5, XH3.P$5
ML2: IC1.17 (O2), XH1.P$4, XH3.P$4
ML3: IC1.16 (O3), XH1.P$3, XH3.P$3
ML4: IC1.15 (O4), XH1.P$2, XH3.P$2
MR1: IC1.14 (O5), XH2.P$5, XH4.P$5
MR2: IC1.13 (O6), XH2.P$4, XH4.P$4
MR3: IC1.12 (O7), XH2.P$3, XH4.P$3
MR4: IC1.11 (O8), XH2.P$2, XH4.P$2
unnamed: R5.2, R5.1.2, U2.CH_PD
unnamed: JP1.1, Z1.+ (1)
unnamed: F1.1, F1.1.1, JP2.2, X1.2, X1.1.1
unnamed: S7.P$4, S7.1.P$4
unnamed: S7.P$5, S7.1.P$5
RAW: C1.1, C1.1.2, C2.2, C3.2, C3.1.2, IC1.10 (CD+), S7.P$2 (O), S7.1.P$2 (O), SV2.1, U6.3 (VIN), XH1.P$1, XH2.P$1, XH3.P$1, XH4.P$1
RST: SV2.3, U2.RST
RX: SV1.2, U2.TX (TXD), U3.2
TX: R2.1, R2.1.1, SV1.1
TX3V3: R2.2, R2.1.2, R3.1, R3.1.2, U2.RX (RXD), U3.1
VIN: D1.C, D1.1.K (C), F1.2, F1.1.2, S7.P$1, S7.P$3 (S), S7.1.P$1, S7.1.P$3 (S)

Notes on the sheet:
Arduino Scocket
Steepers
BUZZ
Bluetooth
Buzz on
NANO
Arduino´s Compatibility
MINI
MICRO
GND
RAW
RST
VCC
D13
D15
D12
D14
D11
D16
D10
Attribution-ShareAlike 4.0 International (CC BY-SA 4.0)
WIFI 802.11
Choose one X.1 = SMD X = THT
XDeSIG
By XDeSIG
Choose one Cx.1 = SMD Cx = THT
000
SCL
SDA
Choose one Rx.1 = SMD Rx = THT
Select 3,3V Arduino Or external
Connector to keypad leds..
to oled I2C...
to Servos, sensors...



Board: 2 copper layers, 50.0 x 50.0 mm, 55 parts (8 on the bottom side), 44 nets.

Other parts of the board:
ESC: ESCORNABOT; ESCORNA_PEQUE
H7: MOUNT-HOLE3.0; 3,0
XDS: XDESIG; XDESIG_CU_2

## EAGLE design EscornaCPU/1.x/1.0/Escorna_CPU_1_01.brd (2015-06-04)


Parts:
C1, C2, C3: 100nF; C1206
C1.1, C2.1, C3.1: C-EU025-024X044; C025-024X044
H1, H2: MOUNT-HOLE3.0; 3,0
IC1: ULN2803; DIL18
JP2: JP2E; JP2
LOGO1: OSHW-LOGOS; OSHW-LOGO-S
PH1, PH2, PH3, PH4: FE15-1; FE15
S1: 10-XX; B3F-10XX
S2: SK12F14F; SK-12F14-G
SV4: MA04-1
U$1: ESCORNABOT; ESCORNA_PEQUE
U$6: XDESIG; XDESIG_CU_2
X3: 22-23-2031
X4: AK500/2
XH1, XH2: B5B-XH-A
Z1: F/CM12P

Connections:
3V3: PH2.14, PH4.14
5V: C3.2, C3.1.2, PH2.4, PH4.4, SV4.4, X3.3
A0: JP2.1, PH2.12, PH4.12
A1: PH2.11, PH4.11
A2: PH2.10, PH4.10
A3: PH2.9, PH4.9
A4: PH2.8, PH4.8, X3.1
A5: PH2.7, PH4.7
A6: PH2.6, PH4.6
A7: PH2.5, PH4.5
AREF: PH2.13, PH4.13
D2: IC1.8 (I8), PH1.5, PH3.5
D3: IC1.7 (I7), PH1.6, PH3.6
D4: IC1.6 (I6), PH1.7, PH3.7
D5: IC1.5 (I5), PH1.8, PH3.8
D6: IC1.4 (I4), PH1.9, PH3.9
D7: IC1.3 (I3), PH1.10, PH3.10
D8: IC1.2 (I2), PH1.11, PH3.11
D9: IC1.1 (I1), PH1.12, PH3.12
D10: JP2.3, PH1.13, PH3.13
D11: PH1.14, PH3.14
D12: PH1.15, PH3.15
D13: PH2.15, PH4.15
GND: C1.2, C1.1.2, C2.1, C2.1.1, C3.1, C3.1.1, IC1.9 (GND), PH1.4, PH2.2, PH3.3, PH3.4, PH4.2, S1.1 (S), S1.2 (S1), S2.P$4, S2.P$5, SV4.3, X3.2, X4.1, Z1.- (2)
MD1: IC1.14 (O5), XH2.P$5
MD2: IC1.13 (O6), XH2.P$4
MD3: IC1.12 (O7), XH2.P$3
MD4: IC1.11 (O8), XH2.P$2
ME1: IC1.18 (O1), XH1.P$5
ME2: IC1.17 (O2), XH1.P$4
ME3: IC1.16 (O3), XH1.P$3
ME4: IC1.15 (O4), XH1.P$2
unnamed: JP2.2, Z1.+ (1)
unnamed: S2.P$3 (S), X4.2
RAW: C1.1, C1.1.1, C2.2, C2.1.2, IC1.10 (CD+), PH2.1, PH4.1, S2.P$1, S2.P$2 (O), XH1.P$1, XH2.P$1
RST: PH2.3, PH4.3, S1.3, S1.4 (P1)
RX: PH1.2, PH3.2, SV4.2
TX: PH1.1, PH3.1, SV4.1

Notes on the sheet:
1.0
Conexión Arduino
Motores
Conector Teclado (3/2)
BUZZ
Bluetooth
RXD
TXD
GND
VCC
Reset
Para PRO_MINI e PRO_MICRO. Conectado a A0
D10 ( NANO )
D10 ( PRO )
SJ_2
Só un condensador C2 é smd, C2.1 THT
Só un condensador C3 é smd, C3.1 THT
Só un condensador C1 é smd, C1.1 THT
Shield
NANO
Arduino
MINI
MICRO
RAW
RST
D13
D15
D12
D14
D11
D16
D10
Creative Commons Recoñecemento 4.0 Internacional (CC BY 4.0)



Board: 2 copper layers, 50.0 x 50.0 mm, 28 parts (5 on the bottom side), 38 nets.

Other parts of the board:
U$2, U$5: ESCORNABOT; ESCORNA_PEQUE
U$3: XDESIG; XDESIG_CU

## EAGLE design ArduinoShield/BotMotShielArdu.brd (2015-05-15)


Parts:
A: 2,15/1,0
B: 2,15/1,0
C: 2,15/1,0
C1: C-EUC1206; C1206
C1.1: C-EU025-024X044; C025-024X044
D: 2,15/1,0
IC1: ULN2803; DIL18
J1, J2, J3, J4: 22-05-7038-03; 7395-03
JP1: JP1E; JP1
JP2: JP2E; JP2
LED: LED5MM
LOGO4: OSHW-LOGOS; OSHW-LOGO-S
RT.1, RT.2, RT.3, RT.4, RT.5, RT.6, RT.7: 10K; 0204/7
S1, S2, S3, S4, S5, S6: B3F-40XX; B3F40XX_NH
S7: 10-XX; B3F-10XX
SH1: ARDUINO_LEONARDO; LEONARDO
SV1: MA06-1
U$1: ESCORNABOT; ESCORNA_PEQUE
U$3: XDESIG1; XDESIG_CU
XH1, XH2: B5B-XH-A
Z1: F/CM12P

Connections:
3V3: JP2.3, SH1.2 (+3V3)
5V: JP2.1, SH1.3 (+5V)
/RST: S7.3, S7.4 (P1), SH1.1 (!RESET)
A0: RT.1.2, SH1.7 (A0)
A1: IC1.8 (I8), SH1.8 (A1)
A2: IC1.7 (I7), SH1.9 (A2)
A3: IC1.6 (I6), SH1.10 (A3)
A4: J4.3, SH1.11 (A4)
A5: J3.3, SH1.12 (A5)
D2: IC1.5 (I5), SH1.15 (2)
D3: SH1.16 (3)
D4: IC1.4 (I4), SH1.17 (4)
D5: JP1.1, SH1.18 (5)
D6: SH1.19 (6)
D7: IC1.3 (I3), SH1.20 (7)
D8: IC1.1 (I1), SH1.21 (8)
D9: IC1.2 (I2), SH1.22 (9)
D10: J1.3, SH1.23 (10)
D11: RT.7.2, SH1.24 (11)
D12: J2.3, SH1.25 (12)
D13: SH1.26 (13)
GND: C.1, C1.1, C1.1.1, D.1, IC1.9 (GND), J1.1, J2.1, J3.1, J4.1, LED.K (C), S1.1 (S), S1.2 (S1), S2.1 (S), S2.2 (S1), S3.1 (S), S3.2 (S1), S4.1 (S), S4.2 (S1), S5.1 (S), S5.2 (S1), S6.1 (S), S6.2 (S1), S7.1 (S), S7.2 (S1), SH1.4 (GND), SH1.5 (GND), SH1.27 (GND), SV1.4, Z1.- (2)
MD1: IC1.14 (O5), XH2.P$5
MD2: IC1.13 (O6), XH2.P$4
MD3: IC1.12 (O7), XH2.P$3
MD4: IC1.11 (O8), XH2.P$2
ME1: IC1.18 (O1), XH1.P$5
ME2: IC1.17 (O2), XH1.P$4
ME3: IC1.16 (O3), XH1.P$3
ME4: IC1.15 (O4), XH1.P$2
unnamed: LED.A, RT.7.1
unnamed: RT.6.1, S6.3, S6.4 (P1)
unnamed: RT.1.1, RT.2.2, S1.3, S1.4 (P1)
unnamed: JP1.2, Z1.+ (1)
unnamed: RT.5.1, RT.6.2, S5.3, S5.4 (P1)
unnamed: RT.4.1, RT.5.2, S4.3, S4.4 (P1)
unnamed: RT.3.1, RT.4.2, S3.3, S3.4 (P1)
unnamed: RT.2.1, RT.3.2, S2.3, S2.4 (P1)
POS: A.1, B.1, J1.2, J2.2, J3.2, J4.2, JP2.2, SV1.5
RAW: C1.2, C1.1.2, IC1.10 (CD+), SH1.6 (+VIN), XH1.P$1, XH2.P$1
RXD: SH1.13 (0), SV1.3
SCL: SH1.32 (D3/SCL)
SDA: SH1.31 (D2/SDA)
TXD: SH1.14 (1), SV1.2

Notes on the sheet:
Só un condensador C1 é smd, C1.1 THT
De Fronte
Esquerda
Dereita
Atrás
Led en placa
BUZZ
Bluetooth
RXD
TXD
GND
VCC
Botons
C. Motores
conectores 3 pines
Indicadores
Pads para pontes (placa a unha cara)
XDeSIG
1514
000



Board: 2 copper layers, 53.3 x 68.6 mm, 37 parts (6 on the bottom side), 39 nets.

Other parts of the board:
U$2: XDESIG1; XDESIG_CU

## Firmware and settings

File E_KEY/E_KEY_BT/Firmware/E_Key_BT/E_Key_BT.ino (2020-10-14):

/*
    Teclado para Escornabot con sensores tipo MakeyMakey na placa E_KEY_BT
    pódese por calquera obxecto que conduza minimamente a corrente,
    axustando o valor umbral: maior para menos sensibilidade
    *
    Necesitamos 2 módulos Bluetooth, un Mestre e outro Escravo. 
    un HC-05 como Mestre e outro escravo que pode ser HC-05 ou HC-06
    
HC-05 como Mestre. 
    Conectaremos o modulo mediante un adaptador USB - RS-232 TTL. Axustes do terminal Baud 38400 ,NL & CR. 
   
    Comandos AT HC-05 (Pulsar reset durante o acendido, (Parpadeo lento)):
    
                Envío               -  Resposta
    test:       AT                  -  OK
    nome:       AT+NAME=<NOME>      -  OK ( preguntar é AT+NAME?, resposta o nome )
    pin         AT+PSWD="<pin>"     -  OK ( AT+PSWD="1234" o mesmo que no escravo)
    Velocidade  AT+UART=9600,0,0    -  OK ( a mesma velocidade que no escravo )
    rol:        AT+ROLE=<rol>       -  OK ( 0=escravo, 1=Mestre (precisa reinicio (pulsar reset mentras se inicia )))
    modo:       AT+CMODE=<mode>     -  OK ( 0=conexión a un enderezo especifico(Bind), 1=conectase o primeiro dispositivo que atopa e se queda ligado a el )
    amarre:     AT+BIND=<enderezo>  -  OK ( Enderezo do escravo no seguinte formato  AT+BIND=98D3,31,7028EF )
    RESET       AT+RESET            -  OK ( Reinicia gardando os datos)
    +info: https://goo.gl/YTYMmm
HC-06 escravo. 
     Conectaremos o modulo mediante un adaptador USB - RS-232 TTL. Axustes do terminal Baud 9600, sen axuste de liña ou NL & CR, NESTE CASO RESPONDE OS COMANDOS DOS HC05.
                Envío             -  Resposta
    test:       AT                -  OK
    nome:       AT+NAME<NOME>     -  OKsetname
    pin         AT+PIN<pin>       -  OKsetPIN ( AT+PIN1234 o mesmo pin que no mestre )
    Velocidade  AT+BAUD4          -  OK9600 ( 4 = 9600 baud ( a mesma velocidade que no mestre ))
    
    XDeSIG 2018 Creative Commons BY-SA4.0.
*/

// A2 Entrada tecla leste (e)
// A7 Entrada tecla oeste (o)
// A6 Entrada tecla norte (n)
// A8 Entrada tecla sur (n)

// A3 Entrada tecla executa (g)

#define led 11 //led para indicar o funcionamento

int entradas [5] = {A0, A2, A3, A4, A5};      //os pines de entrada
char teclas [5] = {'e','n','w','s','g'};  //cadea a enviar vía serie o escornabot


int umbral = 1000;   //Valor a partires do cal se detecta pulsacion ( sensibilidade)
int valor = 0;      //Variable para al macenar o valor da lectura analoxica

int contador = 0;   //Variable do contador

void setup() {
  
  Serial.begin(9600);   //activación da canle serie a 9600bps
  Serial1.begin(9600);   //activación da canle serie 1 a 9600bps

  
 // configuración dos pines de entrada
  for (contador = 0 ; contador < 6; contador ++) {
    pinMode(entradas[contador], INPUT);
  }

// configuración dos pines de saida ( leds)
    pinMode(led, OUTPUT);
  }
 
 
  void loop() {

    for (contador = 0 ; contador < 5; contador ++) {
      
      valor = analogRead(entradas[contador]);     //Collemos valor da entrada correspondente
      
      if (valor > umbral) {                       //Comprobamos se o valor supera o umbral de sensibilidade
        
        Serial1.print (teclas [contador]);         //Enviamos o comando da tecla seguido do retorno de carro
         Serial1.print ("\n");
        
        Serial.print ("Enviando: ");
          Serial.println (teclas [contador]);
        
        Serial.print ("Lectura: ");
          Serial.println (valor);
        
        digitalWrite (led, HIGH);
        delay(200);
        digitalWrite (led, LOW);
        delay(500);
      }
      delay(1); //Retardo entre lecturas
    }

  }

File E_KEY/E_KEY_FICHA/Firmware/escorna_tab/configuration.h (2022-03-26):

#ifndef _CONFIGURATION_H
#define _CONFIGURATION_H

// common interface
#define PIN_BTN1 2
#define PIN_LED1 16
#define PIN_BUZZ 15
#define PIN_LINK 17

// 9 pins by row (3 tabs)
#define PIN_TAB_1_1 14
#define PIN_TAB_1_2 3
#define PIN_TAB_1_3 4
#define PIN_TAB_2_1 5
#define PIN_TAB_2_2 6
#define PIN_TAB_2_3 7
#define PIN_TAB_3_1 8
#define PIN_TAB_3_2 9
#define PIN_TAB_3_3 10

// connected rows (3 tabs by row)
#define ROW_ACTIVATION_MILLIS 100
#define ROW_COUNT 2
#define PIN_ROW_1 11 // 1ª fichas
#define PIN_ROW_2 13 // 2ª fichas
#define PIN_ROW_3 12 // non usada en 6 fichas
/*
#define PIN_ROW_1 12
#define PIN_ROW_2 11
#define PIN_ROW_3 13
*/

/* generic codes
#define CODE_0 "000"
#define CODE_1 "001"
#define CODE_2 "010"
#define CODE_3 "011"
#define CODE_4 "100"
#define CODE_5 "101"
#define CODE_6 "110"
#define CODE_7 "111"
#define TAB_SEPARATOR "-"
#define ROW_SEPARATOR ""
#define PRG_SEPARATOR "\n"

**/
// escornabot codes
#define CODE_0 ""
#define CODE_1 "E\n"
#define CODE_2 "s\n"
#define CODE_3 "e\n"
#define CODE_4 "W\n"
#define CODE_5 "n\n"
#define CODE_6 "w\n"
#define CODE_7 "G\n"
#define TAB_SEPARATOR ""
#define ROW_SEPARATOR ""
#define PRG_SEPARATOR "g\n"
//*

#endif // _CONFIGURATION_H

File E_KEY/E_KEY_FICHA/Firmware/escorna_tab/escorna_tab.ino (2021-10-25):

/*
    Copyright (C) 2020  Rafa Couto <caligari@treboada.net>

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
    You should have received a copy of the GNU General Public License
    along with this program.  If not, see <https://www.gnu.org/licenses/>.
*/

#include <Arduino.h>

#include "configuration.h"
#include "EscornaTab.h"

// EscornaTab configuration
static const EscornaTab::Config cfg =
{
    buttonPin: PIN_BTN1,
    led1Pin:   PIN_LED1,
    buzzerPin: PIN_BUZZ,
    linkPin:   PIN_LINK,
    tabPins:
    {
        PIN_TAB_1_1, PIN_TAB_1_2, PIN_TAB_1_3,
        PIN_TAB_2_1, PIN_TAB_2_2, PIN_TAB_2_3,
        PIN_TAB_3_1, PIN_TAB_3_2, PIN_TAB_3_3,
    },
    rowPins: { PIN_ROW_1, PIN_ROW_2, PIN_ROW_3 }
};


// EscornaTab instance
EscornaTab escorna_tab(cfg, Serial);


void setup()
{
    // initialize serial stream before escorna_tab.init()
    Serial.begin(9600);

    escorna_tab.init();
}


void loop()
{
    // main loop
    escorna_tab.update();
}

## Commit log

2015-05-12 Escorna CPU 1.0
    Vesion para pinchar Arduinos NANO e MICRO
2015-05-12 Borrado os ficheiros non necesarios
    [Escorna_CPU_1_0.brd, Escorna_CPU_1_0.sch]
2015-05-12 Revert "Borrado os ficheiros non necesarios"
    This reverts commit f0e8e139e9fdb07a18cae6f65af2a35986a8202c.
    [Escorna_CPU_1_0.brd, Escorna_CPU_1_0.sch]
2015-05-12 Revert "Revert "Borrado os ficheiros non necesarios""
    This reverts commit 489b6fce32a890dd59943b3321fc677716cee3f6.
    [Escorna_CPU_1_0.brd, Escorna_CPU_1_0.sch]
2015-05-15 engadidos
    novas placas engadidas
    [BotMotShielArdu.brd, BotMotShielArdu.sch, Escorna_Shield_botoneira_2_0B.brd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]
2015-05-15 Esquema actualizado
    [Escorna_Shield_botoneira_2_0B.sch]
2015-05-16 Proposta CERVUS 1.0
    Escorna cpu 2.01 a Cervus 1.0. Pendente de test!
    [Escorna_CPU_2_01.brd, Escorna_CPU_2_01.sch]
2015-06-03 Melloras
    Melloras Botoneira a 2.0C
    CPU a 1.01
    [Escorna_CPU_1_01.brd, Escorna_CPU_1_01.sch, Escorna_Shield_botoneira_2_0B.brd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]
2015-06-03 Pedir placas en IMALL
    procedemento para pedir placas en IMall
2015-06-04 Xdesig update 2015-06-04
    [Escorna_CPU_1_01.brd, Escorna_CPU_1_01.sch]
2015-07-22 Version D
    [Escorna_Shield_botoneira_2_0D.brd, Escorna_Shield_botoneira_2_0D.sch]
2015-07-22 Versión 2.0D
    [Escorna_Shield_botoneira_2_0D.brd, Escorna_Shield_botoneira_2_0D.sch, Escorna_Shield_botoneira_2_0D.stl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]
2015-07-22 Actualización nome
    comprobado e funcional
    [Cervus_1_0.brd, Cervus_1_0.dxf, Cervus_1_0.sch]
2015-08-04 Placa unificada
    Soporte para arduino (nano...) e Teclado nunha PCB
    [Escorna_CPU_2_00.brd, Escorna_CPU_2_00.sch, Escorna_CPU_2_00_3D.stl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]
2015-09-19 Act. bottom layer
    [Escorna_CPU_2_00.brd, Escorna_CPU_2_00.sch]
2015-09-22 Act. slikscreen
    [Escorna_CPU_2_00.brd, Escorna_CPU_2_00.sch]
2015-10-27 error in layer top resolve
    [Escorna_CPU_2_00_BOM.ods, Escorna_CPU_2_01.brd, Escorna_CPU_2_01.sch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]
2015-10-27 "D" Version
    3mm holes
    [Escorna_Shield_botoneira_2_0D.brd, Escorna_Shield_botoneira_2_0D.sch, Escorna_Shield_botoneira_2_0D.stl]
2015-10-28 isolate to 0.4mm
    facility to DiY
2015-11-19 Act S6 library
    [Escorna_CPU_2_01.brd, Escorna_CPU_2_01.sch]
2015-11-21 Actualizando a 2.0
    [Cervus_1_0.brd, Cervus_1_0.dxf, Cervus_1_0.sch]
2015-11-21 Cervus 2.0
    [cervus_2_0.brd, cervus_2_0.sch, cervus_2_0_TCream.dxf]
2016-04-13 New EscornaBot CPU 2.10
    [Escorna_CPU_2_01.brd, Escorna_CPU_2_10.brd, Escorna_CPU_2_10.sch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]
2016-07-29 new values
    New values of resistors, (R5) for the switch S5 and (R10) improves the
    brightness of the green LED.
    [Escorna_CPU_2_10.brd, Escorna_CPU_2_10.sch, Escorna_CPU_2_10_BOM.csv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]
2017-02-23 Directories refactoring.
    [BotMotShielArdu.brd, BotMotShielArdu.sch, Escorna_CPU_1_01.brd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]
2017-02-23 Board credits.
2017-06-11 EscornaCPU 2.12 by XDesig.
    [Escorna_CPU_2_12.brd, Escorna_CPU_2_12.sch]
2018-04-19 New design
    [Escorna_CPU_1_20.brd, Escorna_CPU_1_20.sch]
2018-04-19 Add Keypad 2.1
    [E_KEYPAD__2_1.brd, E_KEYPAD__2_1.sch, Escorna_Shield_botoneira_2_0D.brd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]
2018-04-29 New docus
    [Escorna_CPU_1_20.brd, Escorna_CPU_2_12.brd]
2018-05-05 Attribution-ShareAlike 4.0 International (CC BY-SA 4.0)
    [Escorna_CPU_2_12_BOM.csv, Escorna_CPU_2_12_BOM.ods, Escorna_CPU_2_20.brd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]
2018-07-05 Upgrade
    cambios en 2.20
    [Escorna_CPU_2_12_BOM.csv, Escorna_CPU_2_12_BOM.ods, Escorna_CPU_2_20.brd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]
2018-07-05 Upgrade
    Resolve bug
    [Escorna_CPU_2_20.brd, Escorna_CPU_2_20.sch]
2020-10-14 Up 2.40
    [Escorna_CPU_2_40Amt.brd, Escorna_CPU_2_40Amt.sch, Escornabot_HFD_BOM_SMD.ods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]
2023-03-12 Update links
    [Escorna_CPU_2_12_BOM.ods]

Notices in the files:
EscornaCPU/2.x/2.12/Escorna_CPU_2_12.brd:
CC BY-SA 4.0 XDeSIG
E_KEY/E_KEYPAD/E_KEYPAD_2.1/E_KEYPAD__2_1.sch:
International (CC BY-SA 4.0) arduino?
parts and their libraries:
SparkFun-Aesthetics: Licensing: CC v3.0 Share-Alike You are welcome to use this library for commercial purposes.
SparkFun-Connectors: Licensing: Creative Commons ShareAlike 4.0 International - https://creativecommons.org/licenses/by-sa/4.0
